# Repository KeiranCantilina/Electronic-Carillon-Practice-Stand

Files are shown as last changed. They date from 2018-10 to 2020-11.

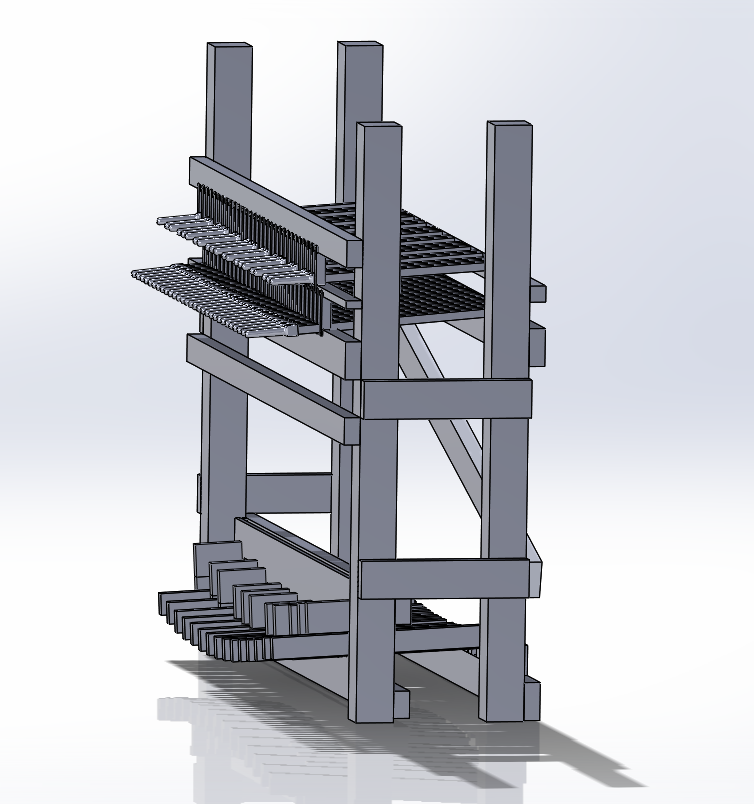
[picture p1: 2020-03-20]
mockup 2.PNG

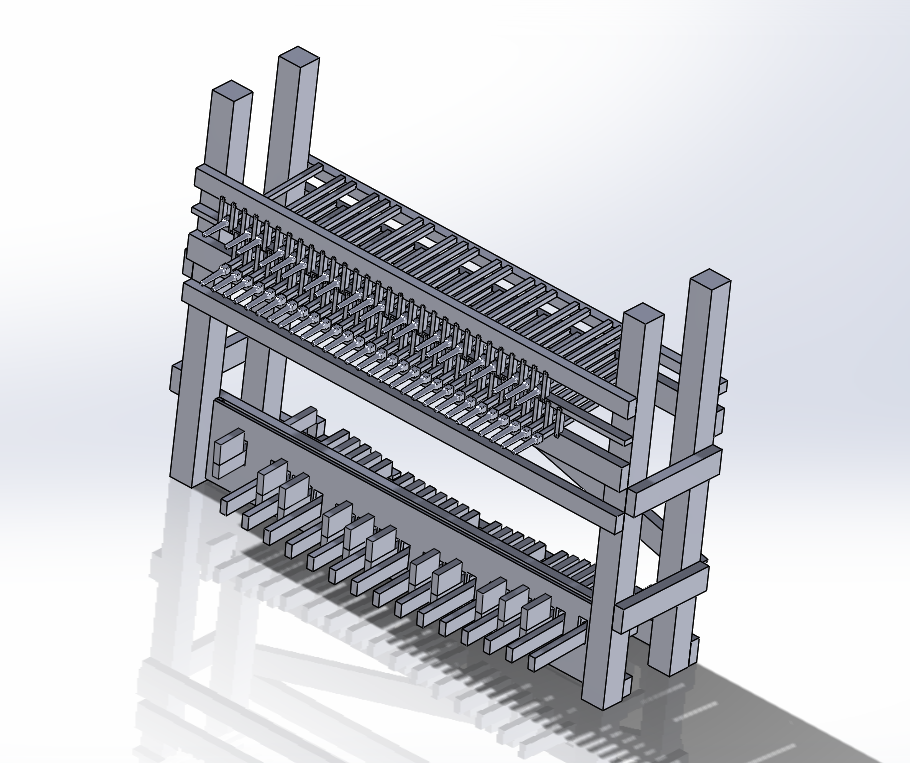
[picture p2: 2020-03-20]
mockup 1.PNG

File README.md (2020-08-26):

# Electronic Carillon Practice Stand
Development of an electronic carillon practice stand with improved dynamic sensitivity and low construction cost.

The performance goals of this project will be considered achieved if a 4-octave digital instrument is built with superior and adjustable dynamic sensitivity compared to existing commercial solutions. Good control of tremelando must be possible. 
The cost optimization goals of this project will be considered complete if the construction is finished at a total cost under $1000 USD (including the cost of purchasing the tools).

The design uses dimensional lumber for the frame and #4 steel rebar for keyweights to reduce costs. 
Given my lack of woodworking or machining skills (and lack of space/money for tools to develop such skills), custom parts are designed to be 3D printable using any low-cost hobbyist 3D printer. All other parts are sourced either online (Ebay, Amazon, Aliexpress, etc.) or at Home Depot.

For the frame, no tools are strictly required other than a handsaw, hacksaw, screwdriver, and measuring tape (unless you count the 3D printer). However, an impact driver saves a lot of time when putting screws in, and 42" Harbor Freight bolt cutters rigged with a double tackle make much quicker work of cutting rebar than a hacksaw. A cheap plastic miter box ($10 at the time of writing) is also helpful.

The current electronic design uses an Arduino Mega 2560 development board, ADS1118 analog-to-digital converters, and SS49E Hall Effect sensors paired with magnets to sense velocity (using magnetic field strength measurements as a proxy for position). A soldering iron is necessary to assemble the electronic components (for now, until I get PCB designs set up after which "toaster oven reflow" might be possible).

The microcontroller sends out MIDI messages over serial-USB to an ancient netbook running virtual midi port software and a sequencer (SyFonOne loaded with a custom soundfont made with recorded samples).

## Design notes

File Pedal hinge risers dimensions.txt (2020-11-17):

pedal riser dimensions (mm)

Total number of pedals: 27; need 27*24 inches of 1x2 (648", 54 feet)
For: Pedal width: 19 (needs to expand to 30mm with pads)
	Pedal Height (diatonic): 50.8 (actually 38)
	Pedal Height (accidental): 76+38 (3in + 1.5 in)
	Pedal Length (diatonic): 568 (nearly 24 inches)
	Pedal Length (accidental): 454
	Pedal Left Margin (to center of G): 85.45
	Pedal Linear Spacing: 45.23
	C to C: 1266.55
	Slot Size: 85.68 (unpadded)
	Keyfall at spreader: 85.68-38 = 47.68 (will need padding to match manuals)
	Foot contact part length: 110

Radius: 18mm (dia. 36)
CHANGE TO: width 19, length 36, holes for hinge screws and mounting screw
G: 59
Bb: 53
C : 35
C#: 29
D: 24
Eb: 19
E: 14
F: 6
F#: 3
G: 1.5
Ab: 0
A: 0
Bb: 0
B: 0
C: 1.5
C#: 3
D: 6
Eb: 9
E: 14
F: 24
F#: 29
G: 35
Ab: 41
A: 47
Bb: 53
B: 59
C: 71

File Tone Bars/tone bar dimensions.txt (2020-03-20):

Aluminum 6061
3/4in width, 1/8in thickness
(19.05mm, 3.175mm)

12 in 		177.52Hz TEST

Bb2	116.5409Hz	14.8074 inches		8.14407 inches between holes
C3	130.8128Hz	13.9764 inches		7.68702 inches between holes
C4	261.6256Hz	9.8827 inches		5.435485 inches between holes
C5	523.2511Hz	6.9864 inches		3.84252 inches between holes
C6	1046.502Hz	4.9389 inches		2.716395 inches between holes
C7	2093.005Hz	3.4898 inches		1.91939 inches between holes

Centers of keys are 23mm apart
Resonators: 3/4in. CPVC Charlotte Water Pipe (0.715" ID, 0.875" OD)(18.161, 22.225)
Test length: 652.8569 mm (25.70303")[130.8Hz] (adjustable to 662.0045 mm (26.06")[129Hz])
Test key length 2: 178.17592mm [523.25Hz] Pipe: 161.15544mm (cut short)
Use with 3/4 in. CPVC CTS Slip Cap Fitting

VERSION 2 ------------------------------

Bb2 to B4 uses 1/16" thick 3/4" wide aluminum bar.

Bb2	116.5409Hz	265.9888 mm		59.5814912 mm from ends
C3	130.8128Hz	250.952 mm		56.213248 mm from ends
B3	246.9417Hz	182.753 mm		40.936672 mm from ends

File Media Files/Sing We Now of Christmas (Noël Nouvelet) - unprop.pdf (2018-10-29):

2 & 4
b
b ∑ | ∑ | ∑ | ∑ | n | n

SingWe Now of Christmas (Noël Nouvelet)

15th Century French
Arr. KKC '15
œ œ | œ œ | œ œ | œ œ | œ

œ
œ

œ œ œ
œ

œ œ

œ™ œ
œ œ | œ œ
Œ | œ

œ
œ

œ œ œ œ
œ

œnœ
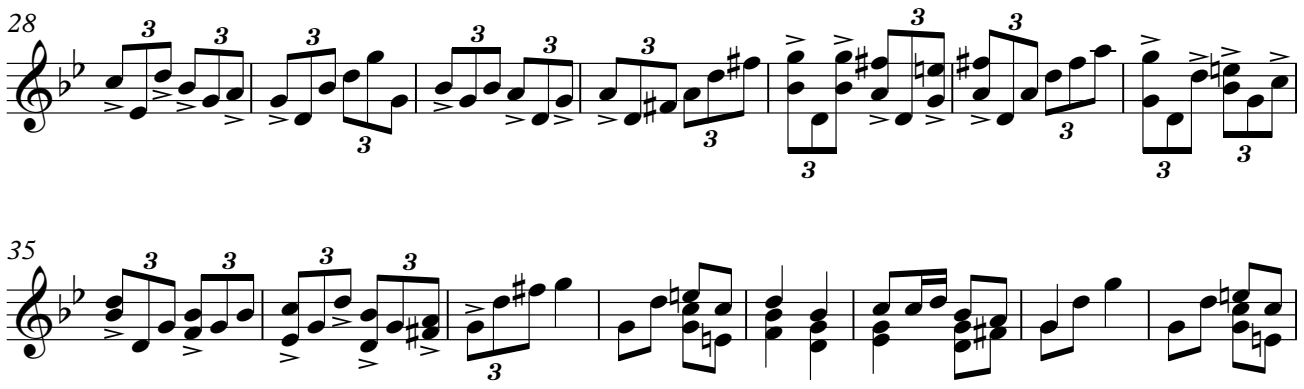
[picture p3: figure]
œœœœ œ; œ œœœ œ

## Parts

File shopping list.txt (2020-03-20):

Shopping List

4* 2x4x10 (cut in half) for posts
4* 2x4x8 for front and side struts (each cut at 70.386 inches, both pieces kept)
1* 2x4x8 for crossbar in back (cut to 6 ft-ish)
3* 2x3x8 for pedalboard, side, and back struts (cut 70.386 inches, as usual)
3* 1x2x8 for key separator, tone bar support, and hammer fulcrum bar (two cut 15.75 in[rest kept], 1 cut 70.386 inches))
1* 2x2x8 for accidental keys hinge base bar (normal 70.386 in cut)

Optional:
1* 4x8 sheet of 1/4" plywood for tone bars (cut down to two 2 x 5.25 foot pieces)
(really what is needed is 7.37" by 5'-3.4" sheet and a 3.87" by 5'-3.4" sheet)
1* 2x4 sheet of 1/2" sanded plywood for pedal keyspreader (cut down to 1ft x 4ft)
(1x3 foot sheet is better for pedalboard)

Lumber Cost
4*4.18	16.72
5*3.02	15.10
3*2.08	06.24
3*2.19	06.57
1*1.98	01.98
--------------
TOTAL:	46.61

Plywood
1*15.22

70.3858268
15.748

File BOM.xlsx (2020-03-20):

Quantity | Item | Price per each | Total Price | Notes | Bought Yet?
1 | 1lb #9 2-1/2" T25 bit wood screws | $10.30 | $10.30 | General assembly screws | Yes
1 | 2-pack of Bosch T25 impact driver bits | $2.38 | $2.38 | I might not actually need these, whoops | Yes
1 | 3/4"x1/8"x3' Aluminum flat bar | $10.00 | $10.00 | Estimated. For tone bar test | Yes
1 | 3/4"x1/16" Aluminum flat bar | $4.58 | $4.58 | Estimated. For tone bar test | Yes
1 | 3/4"x10' CPVC tube | $5.12 | $5.12 | Resonator tube test | Yes
2 | 3/4" CPVC cap | $0.34 | $0.68 | Cap of tubes for test | Yes
2 | Jorgenson 4-in bar clamp | $4.98 | $9.96 |  | Yes
1 | Miter box and saw set | $10 | $10.00 |  | Yes
4
TOTAL | $53.02
YTD | 53.02
Left2Buy | 0

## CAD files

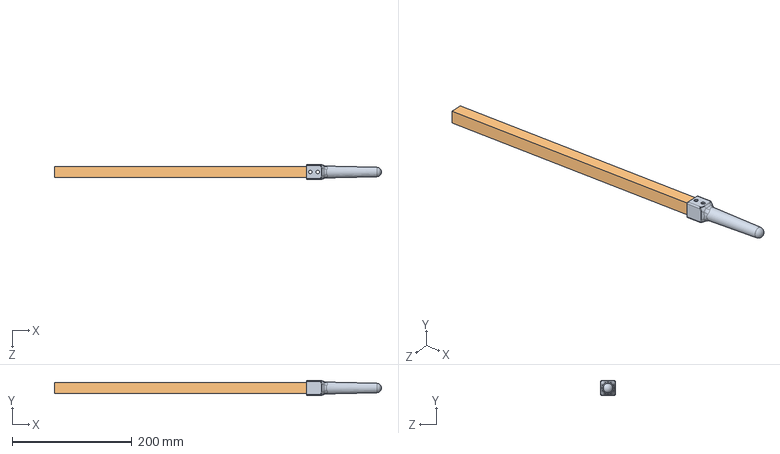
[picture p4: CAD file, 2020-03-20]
Frame/Baton test assembly.SLDASM
546.0 x 25.0 x 25.0 mm
baton
short key stick

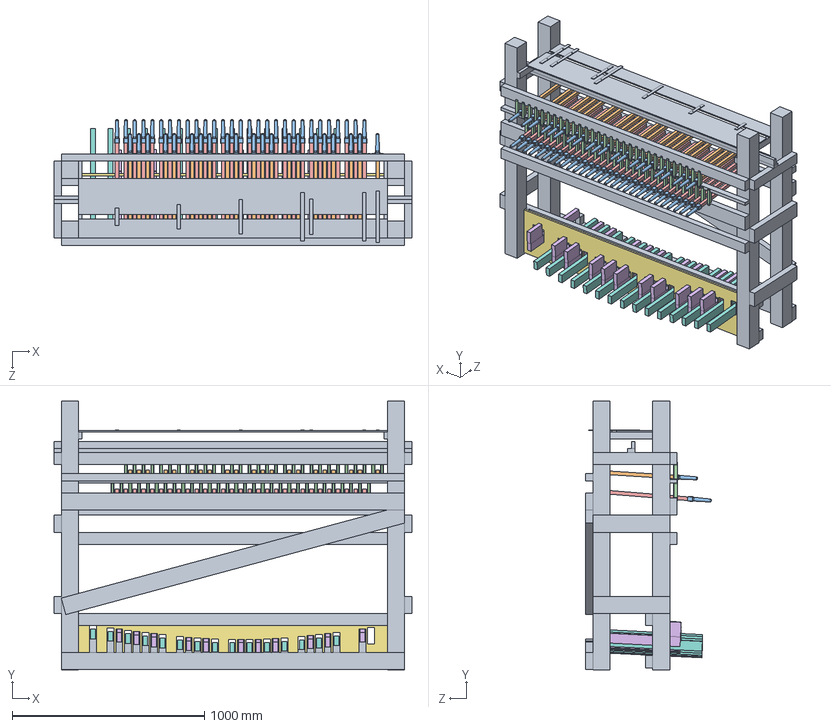
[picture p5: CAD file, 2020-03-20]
Frame/Preliminary test assembly.SLDASM
1863.8 x 1400.0 x 654.5 mm
diatonic keybase
short key stick x 21
baton_alternate x 50
baton spacer x 60
long key stick x 29
short pedal x 11
pedal keybase
long pedal x 15
tone bar mockup_version 3

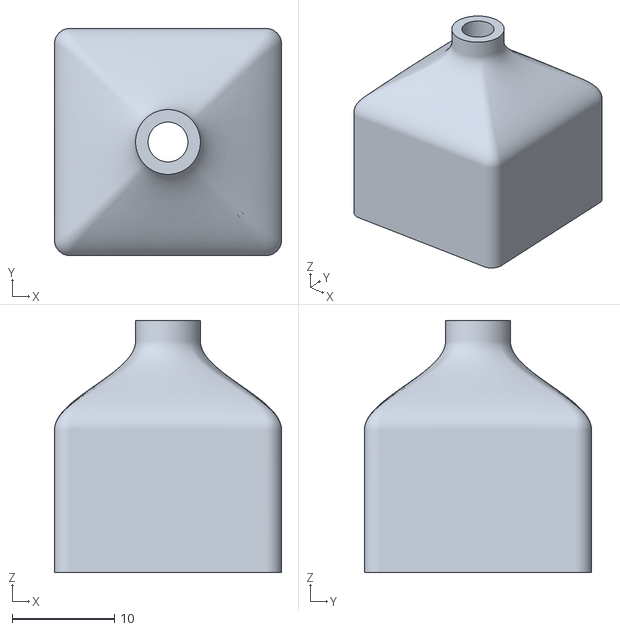
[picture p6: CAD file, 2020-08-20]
3D Printed Components/Hollow Baton Drilling Guide.stl
22.2 x 22.2 x 24.7

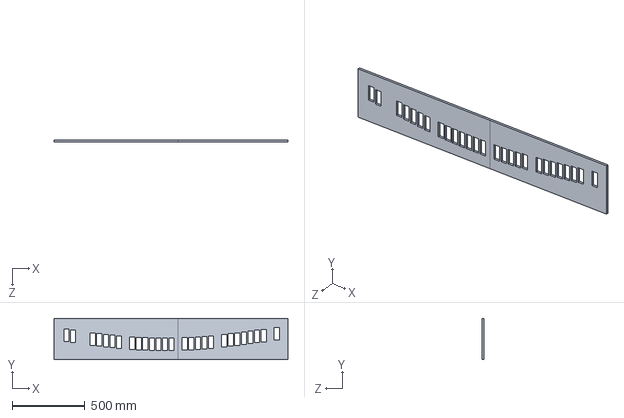
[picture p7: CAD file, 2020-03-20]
Frame/pedal keybase_split1.SLDPRT
1609.8 x 284.7 x 12.7 mm

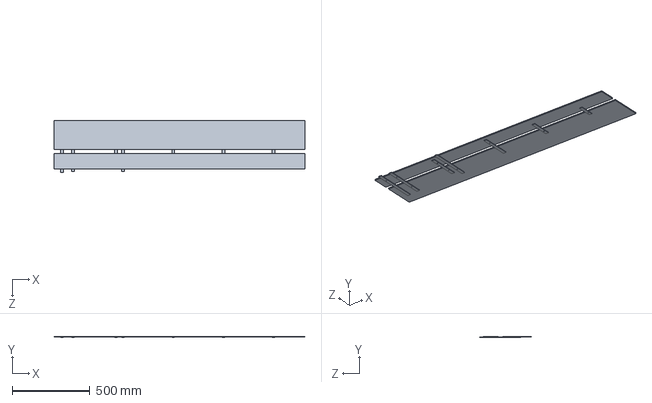
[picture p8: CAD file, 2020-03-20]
Tone Bars/tone bar mockup_version 3.SLDPRT
1610.2 x 9.53 x 333.0 mm

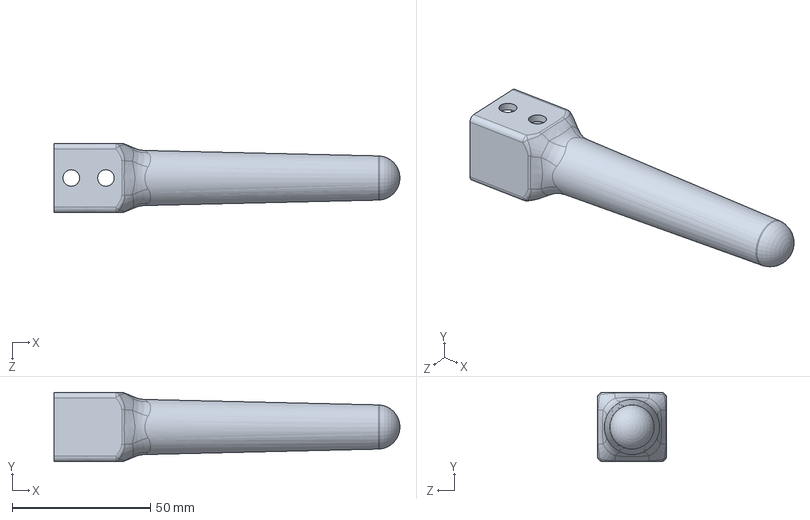
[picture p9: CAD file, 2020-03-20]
Frame/baton.SLDPRT
125.0 x 25.0 x 25.0 mm

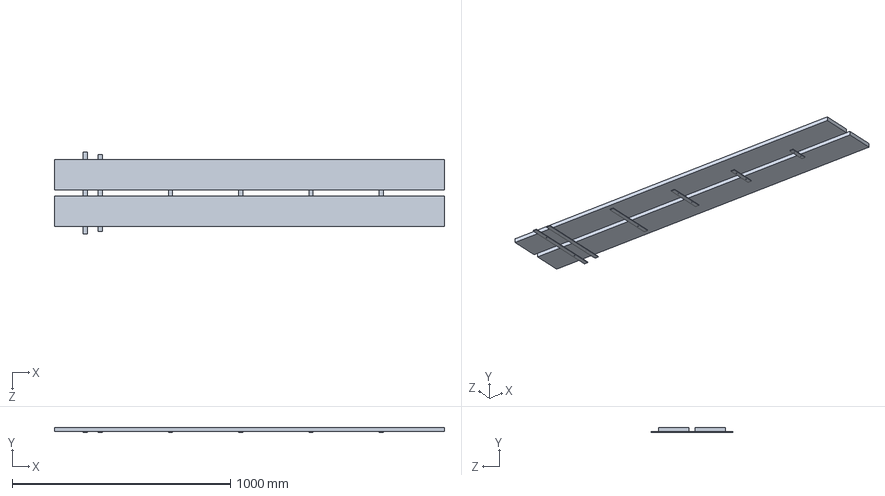
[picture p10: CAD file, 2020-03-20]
Tone Bars/tone bar mockup.SLDPRT
1788.2 x 22.2 x 376.1 mm

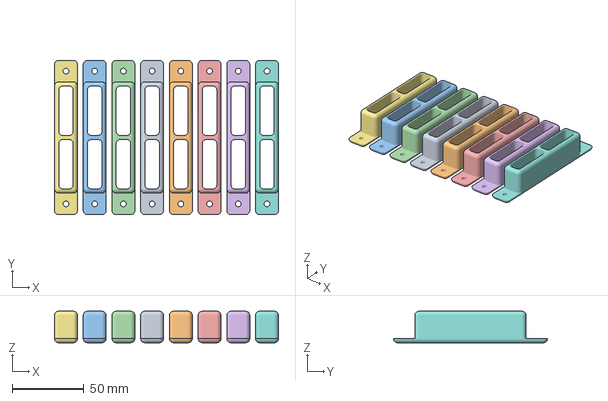
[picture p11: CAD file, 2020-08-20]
3D Printed Components/8X Accidentals Baton Spacer V1.3mf
156.0 x 107.5 x 22.0 mm
Accidentals Baton Spacer V1.stl x 8

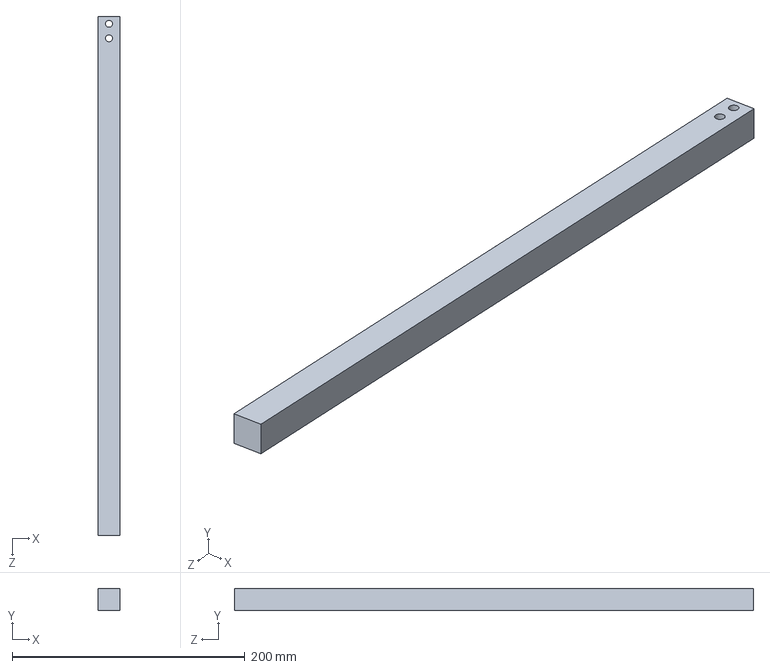
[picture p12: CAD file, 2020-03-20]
Frame/short key stick.SLDPRT
19.0 x 19.0 x 446.0 mm

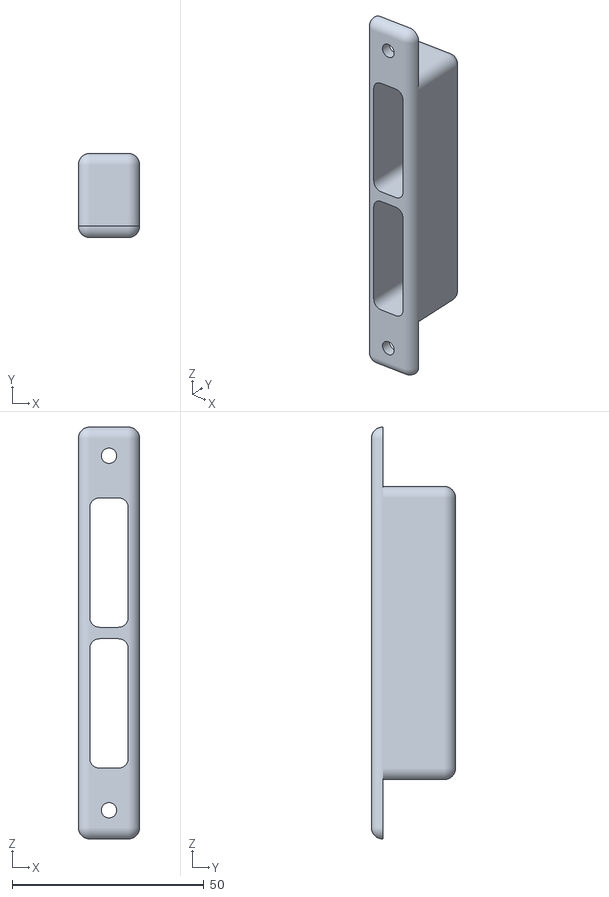
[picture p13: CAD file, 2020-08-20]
3D Printed Components/Accidental Baton Spacer V2 (short).stl
16.0 x 22.0 x 107.5

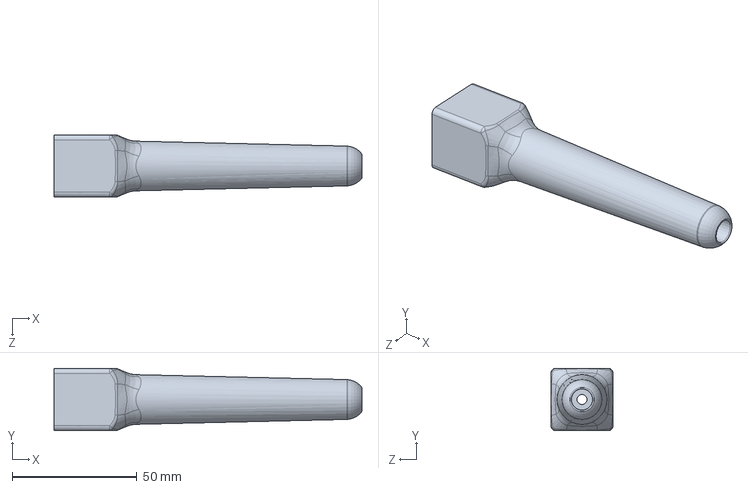
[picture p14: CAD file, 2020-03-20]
Frame/baton_alternate.SLDPRT
123.4 x 25.0 x 25.0 mm

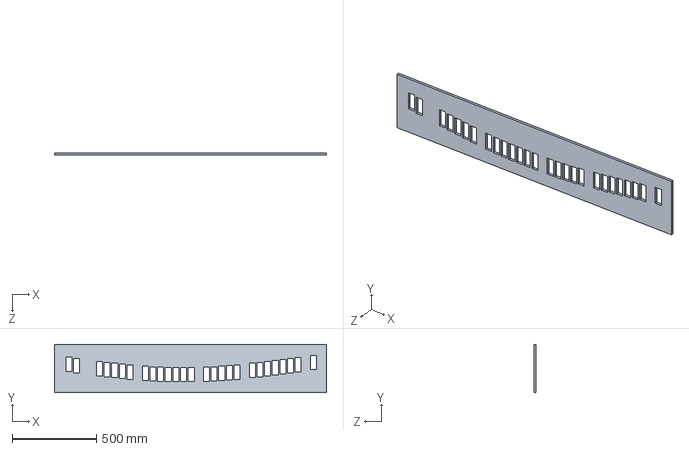
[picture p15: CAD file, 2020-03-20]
Frame/pedal keybase.SLDPRT
1609.8 x 284.7 x 12.7 mm

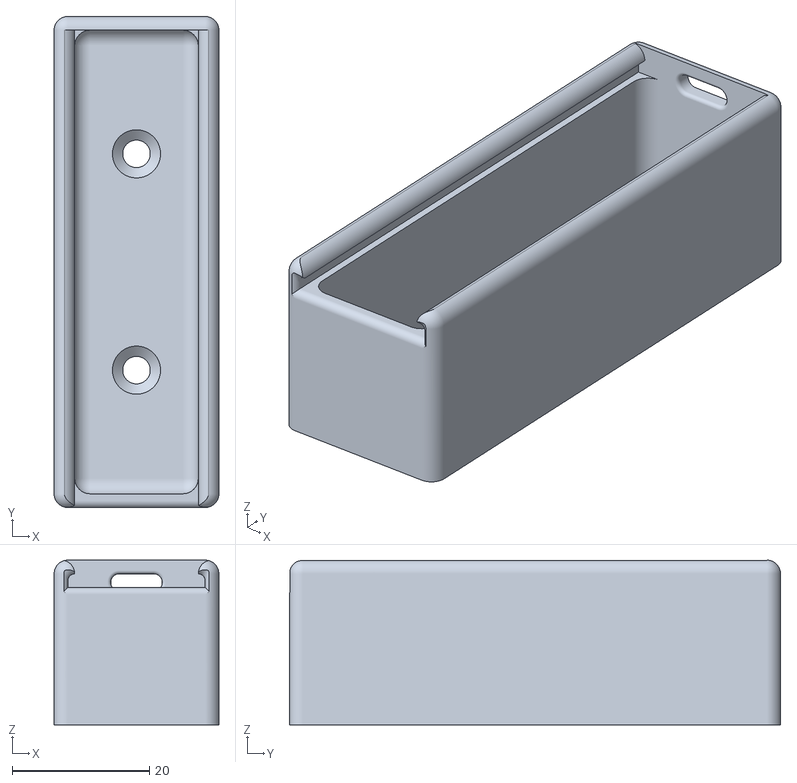
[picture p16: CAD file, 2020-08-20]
3D Printed Components/Weight Container V4.stl
24.0 x 71.5 x 24.0

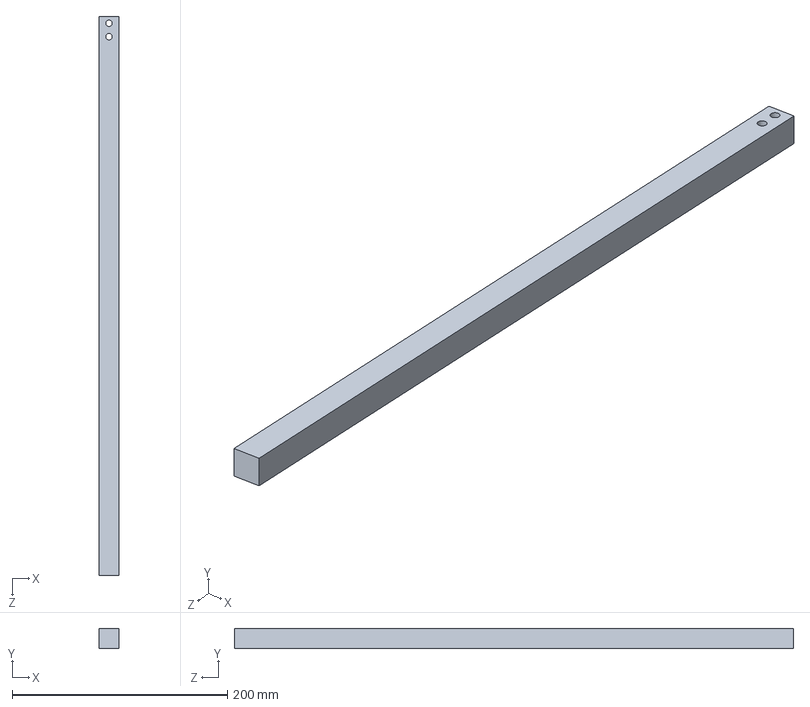
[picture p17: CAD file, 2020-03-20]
Frame/long key stick.SLDPRT
19.0 x 19.0 x 519.0 mm

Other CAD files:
Construction files and doc/batons.dwg
Frame/pedal layout ref.dwg
Frame/keyboard facade_openable.dwg
3D Printed Components/Sensor Holder Test.stl
3D Printed Components/Accidentals Baton Spacer V1.stl
3D Printed Components/Baton Fit Test.stl
3D Printed Components/Baton Hinge Mount V1.stl
3D Printed Components/Baton Hinge Mount V2.stl
3D Printed Components/Baton Spacer Drilling Guide.stl
3D Printed Components/Diatonic Baton Spacer V1.stl
3D Printed Components/Lid Weight Container V1.stl
3D Printed Components/Lid Weight Container V2.stl
3D Printed Components/Lid Weight Container V3.stl
3D Printed Components/Lid Weight Container V4.stl
3D Printed Components/Sensor Holder Test V3.stl
3D Printed Components/Sensor Holder V4.stl
3D Printed Components/Sensor Holder V5.stl
3D Printed Components/Sensor Holder V6.stl
3D Printed Components/Solid Baton V1.stl
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

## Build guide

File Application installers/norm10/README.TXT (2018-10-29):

Readme.txt

(****************************************)
(*                                      *)
(*        SHORT NOTICE                  *)
(*                                      *)
(* Developement of this program is up   *)
(* you! (users) If you want something   *)
(* new you have to send E-Mail. I have  *)
(* few cool ideas, but I don't code 'em *)
(* if there is no users. Let me know if *)
(* you exist :=)                        *)
(*                                      *)
(* -Tommi- The Grape -                  *)
(****************************************)

The WavNormalizer 1.0.4 , build 205 (18. July 2000)
	
	- Now you really can minimize program while process.

The WavNormalizer 1.0.4 , build 204 (17. May 2000)

	- Support for Lame encoder now build in feature.

The WavNormalizer 1.0.4 , build 201

	- "Nag" screen now really is destroyed after "OK"

The WavNormalizer 1.0.4 , build 200
	
	- Corrected many GUI-based bugs
	- Added some GUI features
	- Simplifyed external encoder support
	- Added BladeEnc encoder profile
	- Lots of cleanups to code
	- Correct LinearTeam homepage link

The WavNormalizer 1.0.3 , build 172

	- Corrected startup bug on WinNT with
	  user right.

The WavNormalizer 1.0.2 , build 168

	- Added external command line encoder support
	- Fixed some minor bugs
	- Some minor changes

The WavNormalizer 1.0.0 , build 147
	
	- Optimized normalizatiom engine
	- Rewritten user interface
	- Added 'Normalize' command registration
	  for .Wav files

The WavNormalizer 0.7 PreRelease 3, build 217

	-Huge "What the hell I was thinking about" bug corrected.
	 There was about a 50% chance that a Normalized file was 
	 visited by the "Kellog's Snap, Crackle & Pop" team.
	-My apologies.

The WavNormalizer 0.7 PreRelease 2, build 210
	
	-Wave format bug corrected.

The WavNormalizer 0.7 PreRelease 2, build 208

Content of this file:
	
		Description of program
		System requirements
		Using the program
		License
		Contacting me
		Thanks to
		DISCLAIMER

PROGRAM DESCRIPTION:

	WavNormalizer is a program which will maximize the
	volume of (normalize) Microsoft wave (.wav) files,
	so that they all play at the same volume level. 

	The .wav file has to be 8bit or 16bit wave in PCM
	format in any sample rate, mono or stereo (which is
	actually a normal wave in normal format).

	WavNormalizer normalizes .wav files into themselves,
	therefore no extra hard disk space is needed. However,
	if your system crashes (or if you have a power outtage)
	during the normalization process, the wave file will
	most likely be corrupted. WavNormalizer is quite fast
	(milliseconds in most cases... but minutes could be
	required for files 800Mb or so in length), so the
	risk is really quite small when compared to the
	benefits that you achieve. To be safe, though, you
	might want to copy cherished/irreplaceable .wav files
	to a "working" directory as you modify them, just
	in case.  This action, of course, falls under the
	"common sense" directive as mandated by the ABC
	(Active Brain Cell) branch of life itself. 

System requirements:

        WavNormalizer requires Windows9x, WinNT 4.0 or Win2K.

Using the program:

	In my opinion, this program is so easy to use that
	it doesn´t need any specific help files. Just click
	on "Add files to list" and select the path/file(s)
	that you want to normalize or drag and drop files on
	window.  Then, simply click on the "Go" button.

	Under the Preferences tab, you can select the
	percentage of Normalization by changing the default
	value of 100.0% (either manually by double
	clicking/changing the value, or by using the
	up/down arrows).

	If "Quick Norm" is selected, then WavNormalizer
	will automatically Normalize any .wav file that
	you Drag and Drop onto the program icon.

	If "Hide main window" is selected, then WavNormalizer
	will not show main window during normalization
	(this option requires "Quick norm" option to work).

	Under Enc tab, you can define command line for
	external program. Normalizer will send file to
	program just after normalization. There is few
	details you need to know about how this encoder
	options will effect to commandline.

	Encoder path: 
	
		Path and file name that points your
		encoder executable (.exe) file.

	Encoder command line options:

		This is the "prototype" for your
		commandline that will be formatted
		by normalizer. There is couple things
		you need to put there.

		%inf variable: This variable is
		replaced with normalized file's
		path and name
		
		%outf variable: If you need to
		declare output file name for encoder

	(Like -i:%inf -o:%outf -a - c -SomeOptions ...)
	%inf and %outf variables must be written exactly
	like that (Small letters). You have to declare
	%inf variable!	

	Filename options:

	Extension: If you need to change outfile extension
	it will be replased with extension declared in here

	You can save this settings and and it to ready to
	roll profiles. It is handy if you use more that one
	encoders. (Please send me working profiles via E-mail.
	just send copy of ltn1.ini to me please.)

Licence:

	This program is free for use of any kind. If you
	like and/or use this program, please send me a
	postcard or contact me via Email at the address
	below (or you can contribute actual currency if
	you'd like!? :)

	You may distribute this program freely, as long
	as it is unchanged and includes all of the files
	listed below.

	Norm10.exe	Program
	Readme.txt	This file

Contacting me:

	If you have any suggestions, bugs, or comments
	pertaining to this program, I would be happy to
	hear from you. Here's how you can contact me:

	SnailMail:

		Send Email to find out.

	EMail:
	
		tommi.prami@kno.fi

Thanks to:

	Juha Hartikainen
		-Many programming hints.

	Edmond "Ed" L Lacoste III
		-Graphics design for program	

	JJ Richard
		-Major beta testing and his American
		 English language grammar corrections.
	
	Reijo "Reke" Tuononen
		-For cool (Programming) ideas and he's
		 professional touch :=)
	
	Marko Raninen
		-Many ideas pertaining to user interface.

	Sanna Antikainen
		-For lending me her copy of the Titanic Soundtrack
		(which helped me find that huge bug in build 210).

	all co-workers at KNO Oy...

DISCLAIMER OF WARRANTY: 
(I wish I didn't have to do this, but I must);

	THIS PROGRAM IS DISTRIBUTED AS FREEWARE, SO DON'T
ASSUME A WARRANTY OF ANY KIND. YOU USE THIS PROGRAM COMPLETELY
AT YOUR OWN RISK. DON'T ASSUME CORRECTNESS, ACCURACY OR RELIABILITY
OF ANY KIND WHEN USING THIS DISTRIBUTED SOFTWARE. ANY DAMAGE CAUSED 
BY THIS PROGRAM, WHETHER BEING FROM A DIRECT OR INDIRECT USE OF THIS 
PROGRAM, AS WELL AS TO ANY EQUIPMENT USED, AND/OR ANY MATERIAL IN IT,
IS SOLEY YOUR RESOPONSIBILITY.  THE RISK IS YOURS AND YOURS ONLY.
YOU AGREE TO ALL OF THESE TERMS BY STARTING THIS PROGRAM.  IF YOU 
DON'T AGREE WITH THESE TERMS, THEN DON'T USE THIS PROGRAM.

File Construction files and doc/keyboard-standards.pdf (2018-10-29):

## Appendix D GCNA Keyboard Standards

The following text is reproduced in its entirety from the GCNA Bulletin, November 1970, incorporating several corrections of errata. The standards described herein were adopted at the 1970 Congress and remain the recognized North American carillon clavier standard, except for modifications to the pedals which were approved in 1981. The text in italics has been superceded by revised standards adopted in 1981. The 1981 revisions were never published per se, but exist in the form of drawings prepared by Richard Strauss and dated 1981. Only those dimensions pertaining to pedal geometry were adopted. Copies of these drawings are on file at the Brees Library in Lake Wales, Florida. The drawings following these written standards attempt to graphically illustrate the standards adopted in 1970 and 1981.

Over the years since the adoption of these standards, some carillon designers and builders have introduced refinements and improvements in their claviers, in some cases deviating from the standards. The clavier design by Richard Strauss know as K2000, which incorporates European key spacing, has been used as the basis for several new claviers in the U.S. as well as Europe. These trends indicate that clavier design continues to evolve

## Carillon Console Standards of the Guild of Carillonneurs in North America July 1970

Text in italics superceded by revised standards adopted in 1981

Purpose: | The purpose of this standard is to specify dimensions and construction details for manual consoles of carillons installed in the United States of America and in Canada.
Scope: | This standard shall apply in detail to consoles of carillons of four-octave range. For carillons of more or less than four octaves, this standard shall apply as far as practical, consistent with the different range of the instrument.
1 | Range of Manual: The basic compass of the manual clavier shall be four octaves, c3 to c7. A key shall be provided for each bell in the carillon; all semi-tone keys should be provided within the compass of the instrument.1
2 | Range of Pedals: The basic compass of the pedal clavier shall be two octaves, C3 to C5 including a pedal corresponding to each manual key present within this compass; where bells lower than the basis keynote (the bell attached to c3 key and pedal) are present, extra pedals to control these bells shall be provided below the basic pedal compass.
3 | Lateral relationship of manual to pedal: A “playing axis” has been established in designing the standard keyboard: this axis shall be a vertical line joining the centerlines of the d5 manual key and the B3 pedal; in other words, the B3 pedal is to be located directly beneath the d5 manual key.
4 | The vertical distance from the centerline of “white” keys to top of “white” pedal at axis shall be 30 11/16 in. (779 mm.).
5 | Horizontal distance from front end of pedal to front end of “white” keys at axis shall be 1 3/8 in. (35 mm.).

6 | The vertical distance between centerlines of rows of “white” and “black” keys shall be 3 13/16 in. (97 mm.).
7 | Horizontal distance from front end of “white” key to front of “black” key shall be 2 3/4 in. (70 mm.).
8 | Horizontal distance between key centers shall be 2 in. (51 mm.).
9 | It is recommended that the “white” keys be no shorter than 24 in. (610 mm.), measured from the playing end to the fulcrum.
10 | The keys, when at rest, should be inclined upward slightly toward the playing ends; the centerline of each key should form an angle of 2°to a horizontal line drawn through the center of the key at the fulcrum.
11 | The distance from the front end of the “white” keys to the front surface of the key “spreader” should be not less than 7 ¼ in. (184 mm.).
12 | That untapered portion of the key which lies on the player’s side of the “spreader” shall have a cross-section of 1 in. x 1 in. (25 mm. x 25 mm.).
13 | The tapered playing-end of the key shall have a length of 3 3/8” in. (86 mm.).
14 | Shape of key playing end: The playing end of the key shall be nearly cylindrical, (actually, a truncated cone), being tapered in such a way as to have a diameter of 5/8 in. (16 mm.) at a point 1 ½ in. (38 mm.) from the end; it is suggested that this be produced by giving this portion of the key a diameter of approximately ¾ in. (19 mm.) at the end toward the untapered (square cross-section) portion and 9/16 in. (14 mm.) at the end toward the player. (This requirement, together with the key spacing detailed above, insures that there will be a clear space of 3 3/8 in. (86 mm.) at the measuring point for the hand to descend between the keys on either side of the one being played)
15 | The transition from the square to circular cross-sectional portions of the key shall be smoothed, to present no sharp corners.
16 | The end of the key shall terminate in a portion of a sphere whose diameter is no less than the diameter of the key at that point and no more that 1 ½ times this diameter.
17 | The depth of stroke of the key, measured at the front edge of the key “spreader” shall be 2 in ± 1/8 in. (51 mm. ± 3 mm.)
18 | It is recommended that the length of the “white” pedal at axis be not less than 22 5/8 in. (575 mm.) measured from the front end to the fulcrum.
19 | The top surface of the pedal, when at rest, shall make an angle of 2°with a horizontal line drawn through the top center of the fulcrum.
20 | The vertical distance from the top of the “black” pedal to the top of the adjacent “white” pedal shall be 3 in. (76 mm.). But note, that in the case of the pedals in the range where concavity is used, this distance shall be measured from the top of the “black” pedal to a point half way between the top surfaces of the adjacent “white” pedals.
21 | The horizontal distance between centerlines of adjacent “white” pedals shall be 3 ½ in. (89 mm.), measured at the end of the pedals nearest player. The “black” pedals shall be centered between adjacent “white” pedals.
22 | The width of the pedals shall be 1 3/16 in. (30 mm.).

23 | The effective length of the playing surface of the “white” pedal shall be not less that 4 ¾ in. (121 mm.) nor more than 5 in. (127 mm.), the former being recommended.
24 | The effective length of the playing surface of the “black” pedal should be not less than 4 in. (102 mm.) nor more than 4 ¼ in. (108 mm.), the latter being recommended. N.B.: this dimension shall not overlap the preceding (no. 23) by more than ¼” (6 mm.).
25 | The depth of stroke of the pedal, measured at the pedal “spreader”, shall be 2 in. ± 1/8 in. (51 mm. ± 3 mm.).

26 The pedal clavier (having a compass as detailed in point no. 2 above) is to have a slight
| radiation at the top of the compass and a greater radiation at the bottom. In the case of a four-octave console with no additional pedals below the basic keynote, this radiation is to be as detailed in the accompanying prints; the angle and equivalent radii (approximate) from which these prints where drawn are listed in Table I below:

Table I
Pedal Radiation

Left Radiation
Note | Angle | Equivalent Radius
F#3 | 1 1/2° | 67 ½ in. (1,715 mm.)
F3 | 2° | 61 ½ in. (1,562 mm.)
E3 | 7° | 55 ½ in. (1,410 mm.)
D#3 | 10 1/2° | 49 ½ in. (1,257 mm.)
D3 | 14° | 43 ½ in. (1,105 mm.)
C#3 | 19° | 37 ½ in. (953 mm.)
C3 | 23° | 31 ½ in. (800 mm.)

Right Radiation
Note | Angle | Equivalent Radius
F4 | 2° | 61 ½ in. (1,562 mm.)
F#4 | 3° | 61 ½ in. (1,562 mm.)
G4 | 4° | 61 ½ in. (1,562 mm.)
G#4 | 5° | 61 ½ in. (1,562 mm.)
A4 | 6° | 61 ½ in. (1,562 mm.)
A#4 | 7° | 61 ½ in. (1,562 mm.)
B4 | 8° | 61 ½ in. (1,562 mm.)
C5 | 10° | 61 ½ in. (1,562 mm.)

N.B.: “Angle” is that made by one side of the pedal with a line normal to the pedal “spreader” which passes through the point on that side of the pedal opposite the fulcrum. “Equivalent radii” are measured along the extended centerline of the nearest unradiated pedal key and are measured from the front of the unradiated pedals.

27 The pedal clavier shall be concave, to a large radius at the top end of the compass, and a smaller radius at the bottom, and the concavity shall be similar and complementary to the radiation specified in item no. 26 above. For the four-octave console having no pedals below the basis keynote, the concavity shall be as shown in the accompanying prints, and given in Table II below:

Table II
Pedal Concavity
Left Concavity | | Right Concavity
Note | Elevation | Note | Elevation
F#3 | 1/8 in. (3 mm.) | F4 | 1/8 in. (3 mm.)
F3 | 3 1/6 in. (5 mm.) | F#4 | 1/4 in. (6 mm.)
E3 | ½ in. (13 mm.) | G4 | 3/8 in. (9 mm.)
D#3 | 7/8 in. (22 mm.) | G#4 | 9/16 in. (14 mm.)
D3 | 1 ½ in. (38 mm.) | A4 | 13/16 in. (21 mm.)
C#3 | 2 ¼ in. (57 mm.) | A#4 | 1 in. (25 mm.)
C3 | 3 1/16 in. (78 mm.) | B4 | 1 3/8 in. (35 mm.)
| | C5 | 2 1/8 in. (54 mm.)

N.B.: “Elevation” is the vertical distance of the top of the pedal, when at rest, above the tops of corresponding pedals (“black” or “white”) in the range to which no concavity is applied.
28 | The playing surface of the pedals should be made with a suitable material to minimize
pedal wear.
29 | For carillon consoles large than four octaves, the center axis shall remain the same as for
the four-octave carillon console.
30 | The wire adjusters used must reliably hold the adjustment selected by the carillonneur,
but must be readily capable of adjustment by the carillonneur using one hand while in front of the console.
31 | The wires connecting the “white” keys to the carillon should be attached to the key at a
point no less than 11 in. (279 mm.), or more than 12 in. (305 mm.), from the playing end of the key, and the wire connections to the “black” keys shall be attached at a point no less than 8 ¼ in. (210 mm.) and no more than 9 ¼ in. (235 mm.) from the playing end of the key.
32 | The music rack shall be at least as wide as the distance between the centers of the keys
at the extreme ends of the compass, shall tilt back as far as practical (without touching the wires), and shall not overhang the front edge of the key “spreader”. The height of the rack back shall be 14 in. (356 mm.). The angle between the back and the surface of the lip shall be 90°. The surface of the lip (or ledge) shall be at least 1 ¼ in. (32 mm.) wide, and no wider than 1 ¾ in. (44 mm.).
33 | The bench shall be adjustable for height, shall be provided with a footrest (located far
enough distant from the pedals to give good clearance when playing the pedals), and shall be at least as long as the distance between the last key “spreader” slot on the left and the last pedal “spreader” slot on the right.
34 | It is imperative that the console be constructed in a perfectly sturdy manner; of materials
of a high degree of durability and permanence; accurately to the dimensions given, and allowing an absolute minimum of “play” or waste motion; in such a manner and of such materials as to operate smoothly and reliably in all conditions, with a minimum of adjustment and upkeep; and at the same time, to be as noiseless as possible.

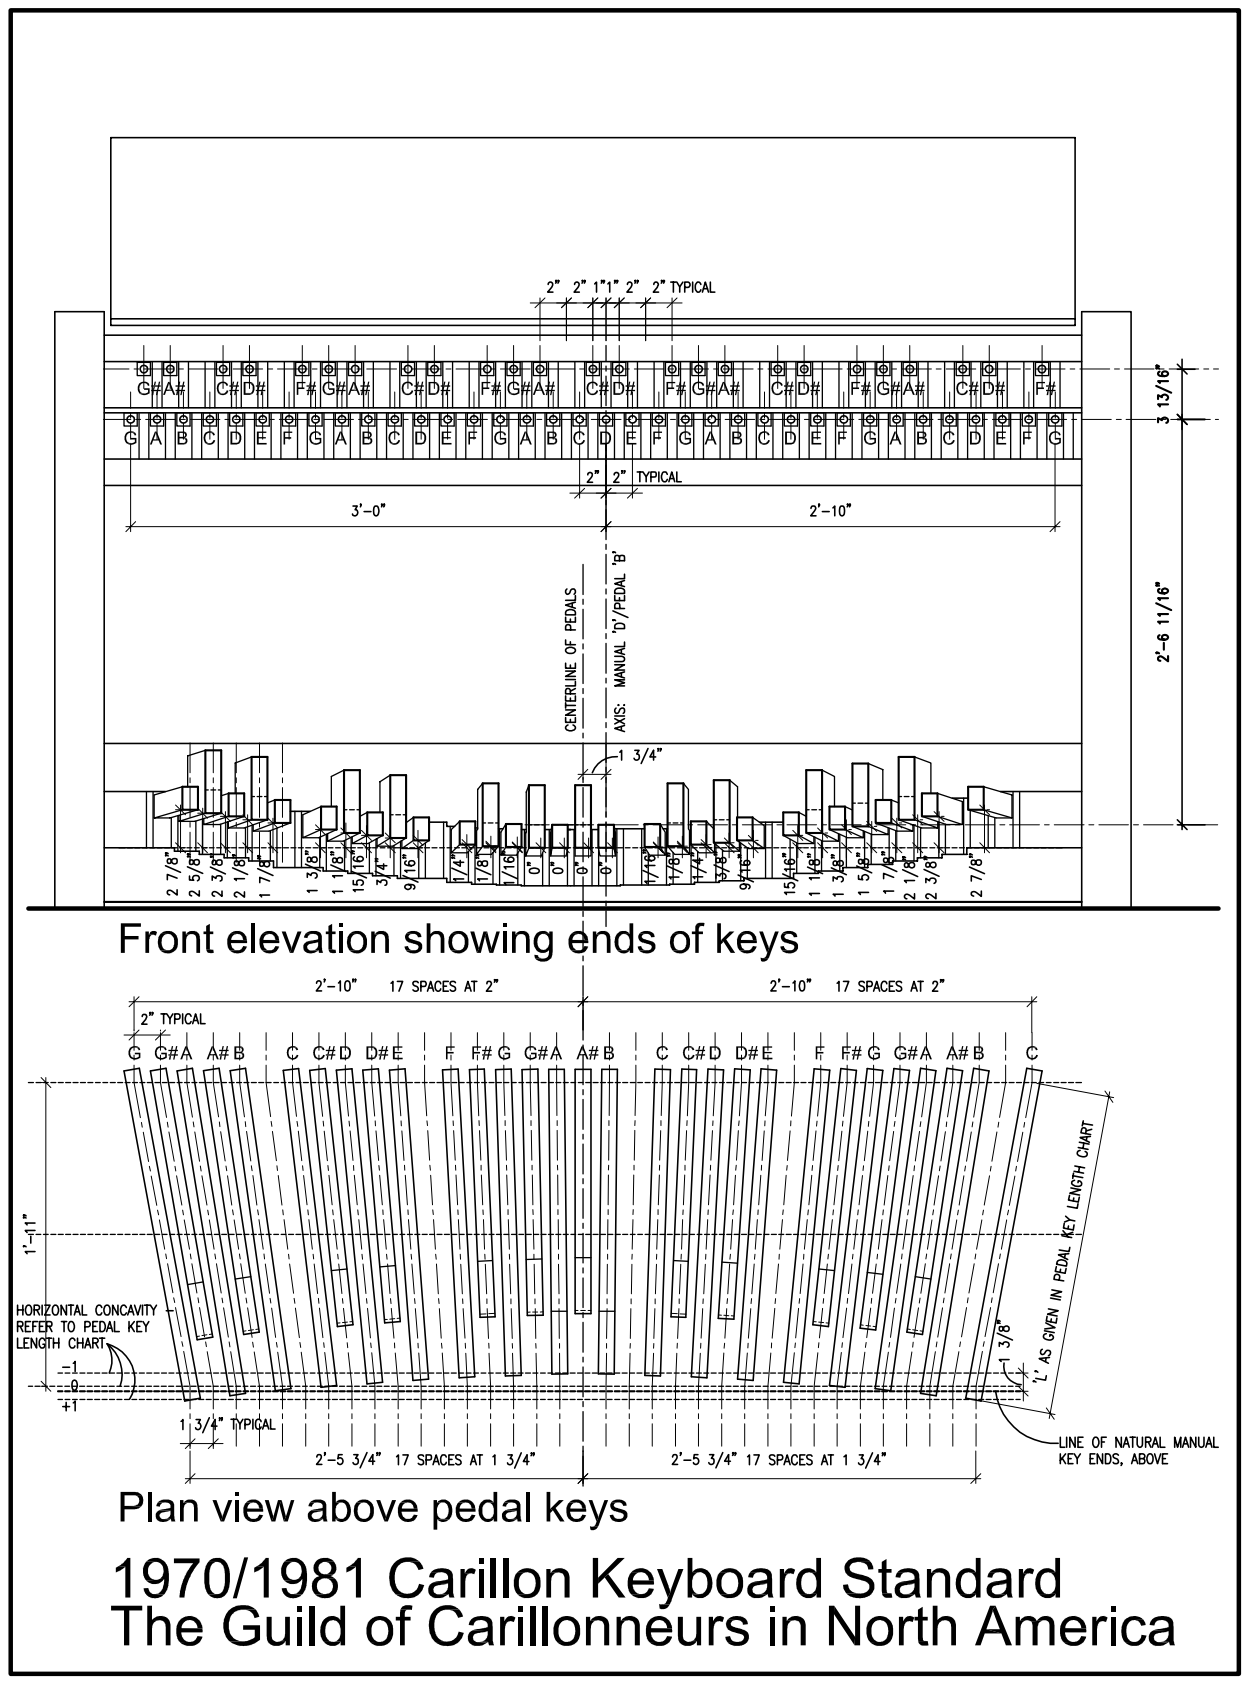
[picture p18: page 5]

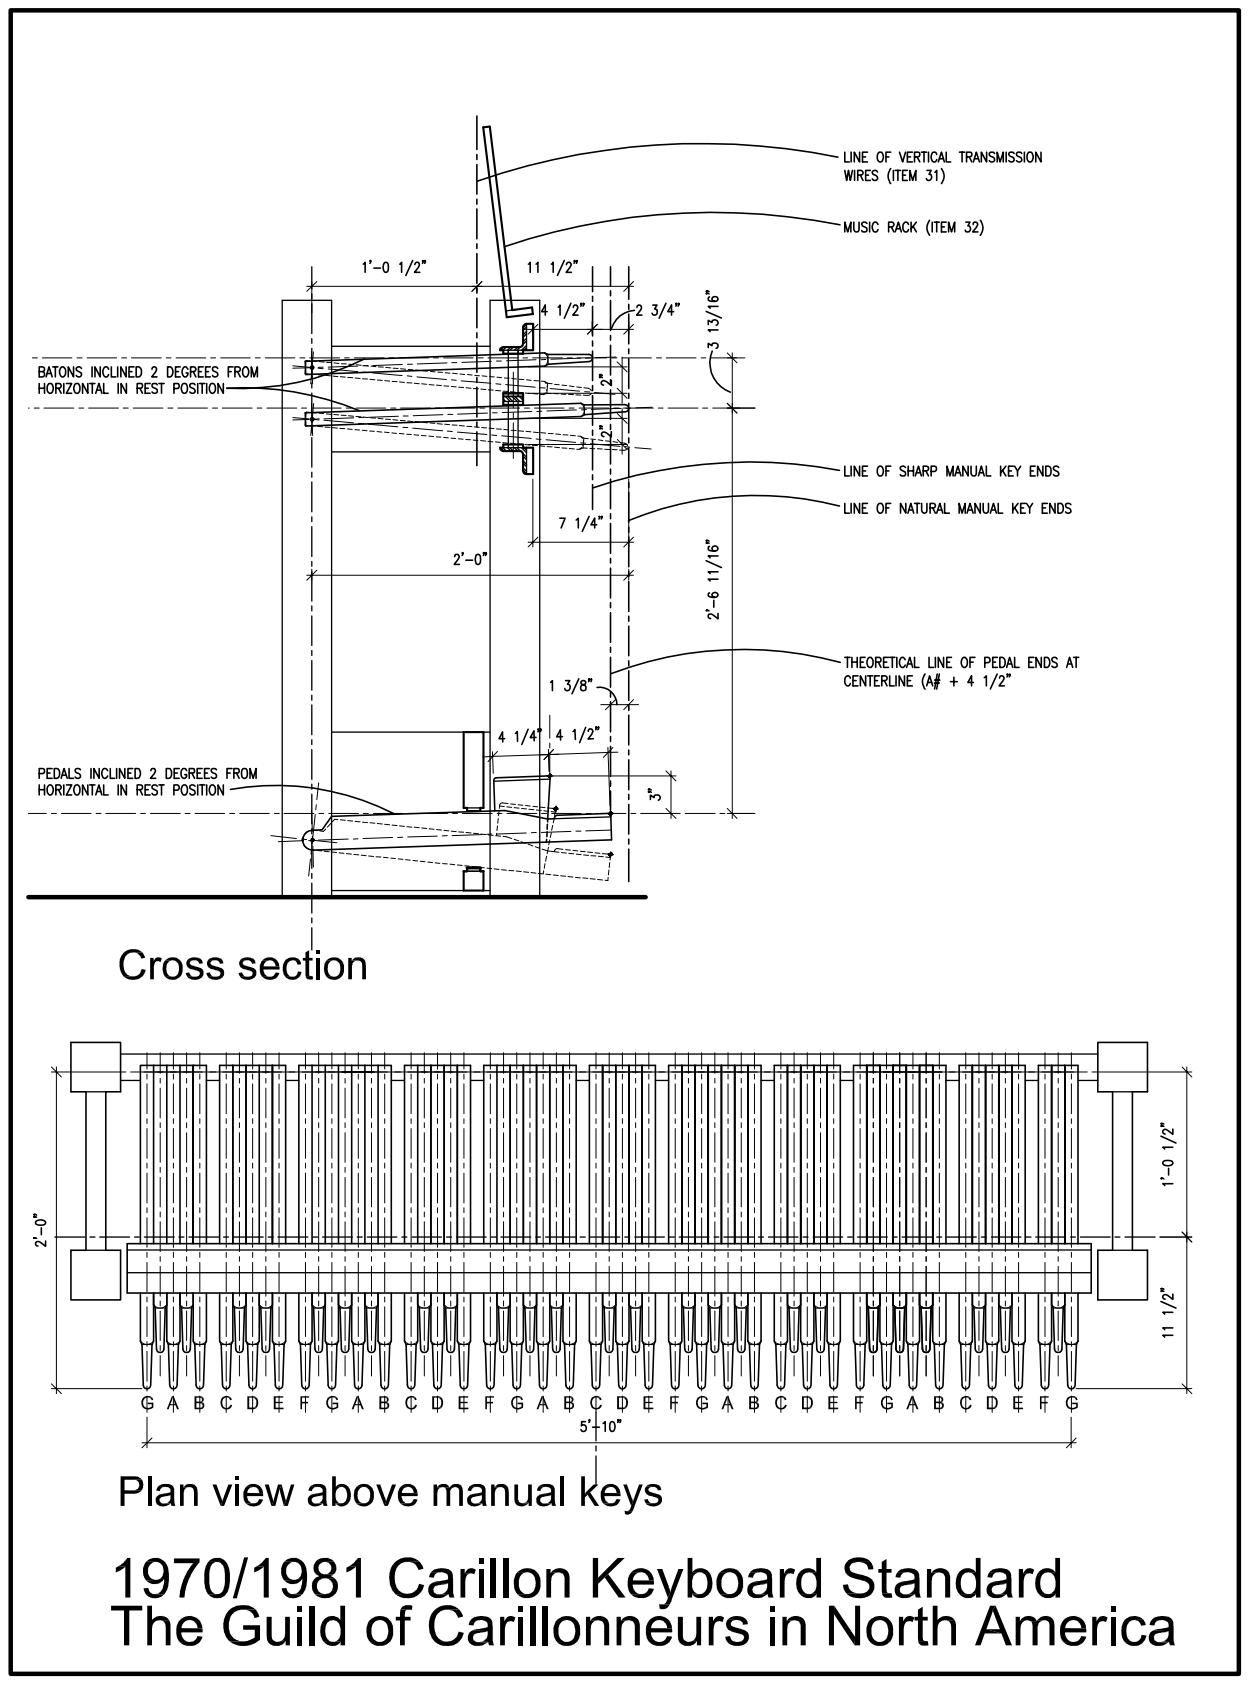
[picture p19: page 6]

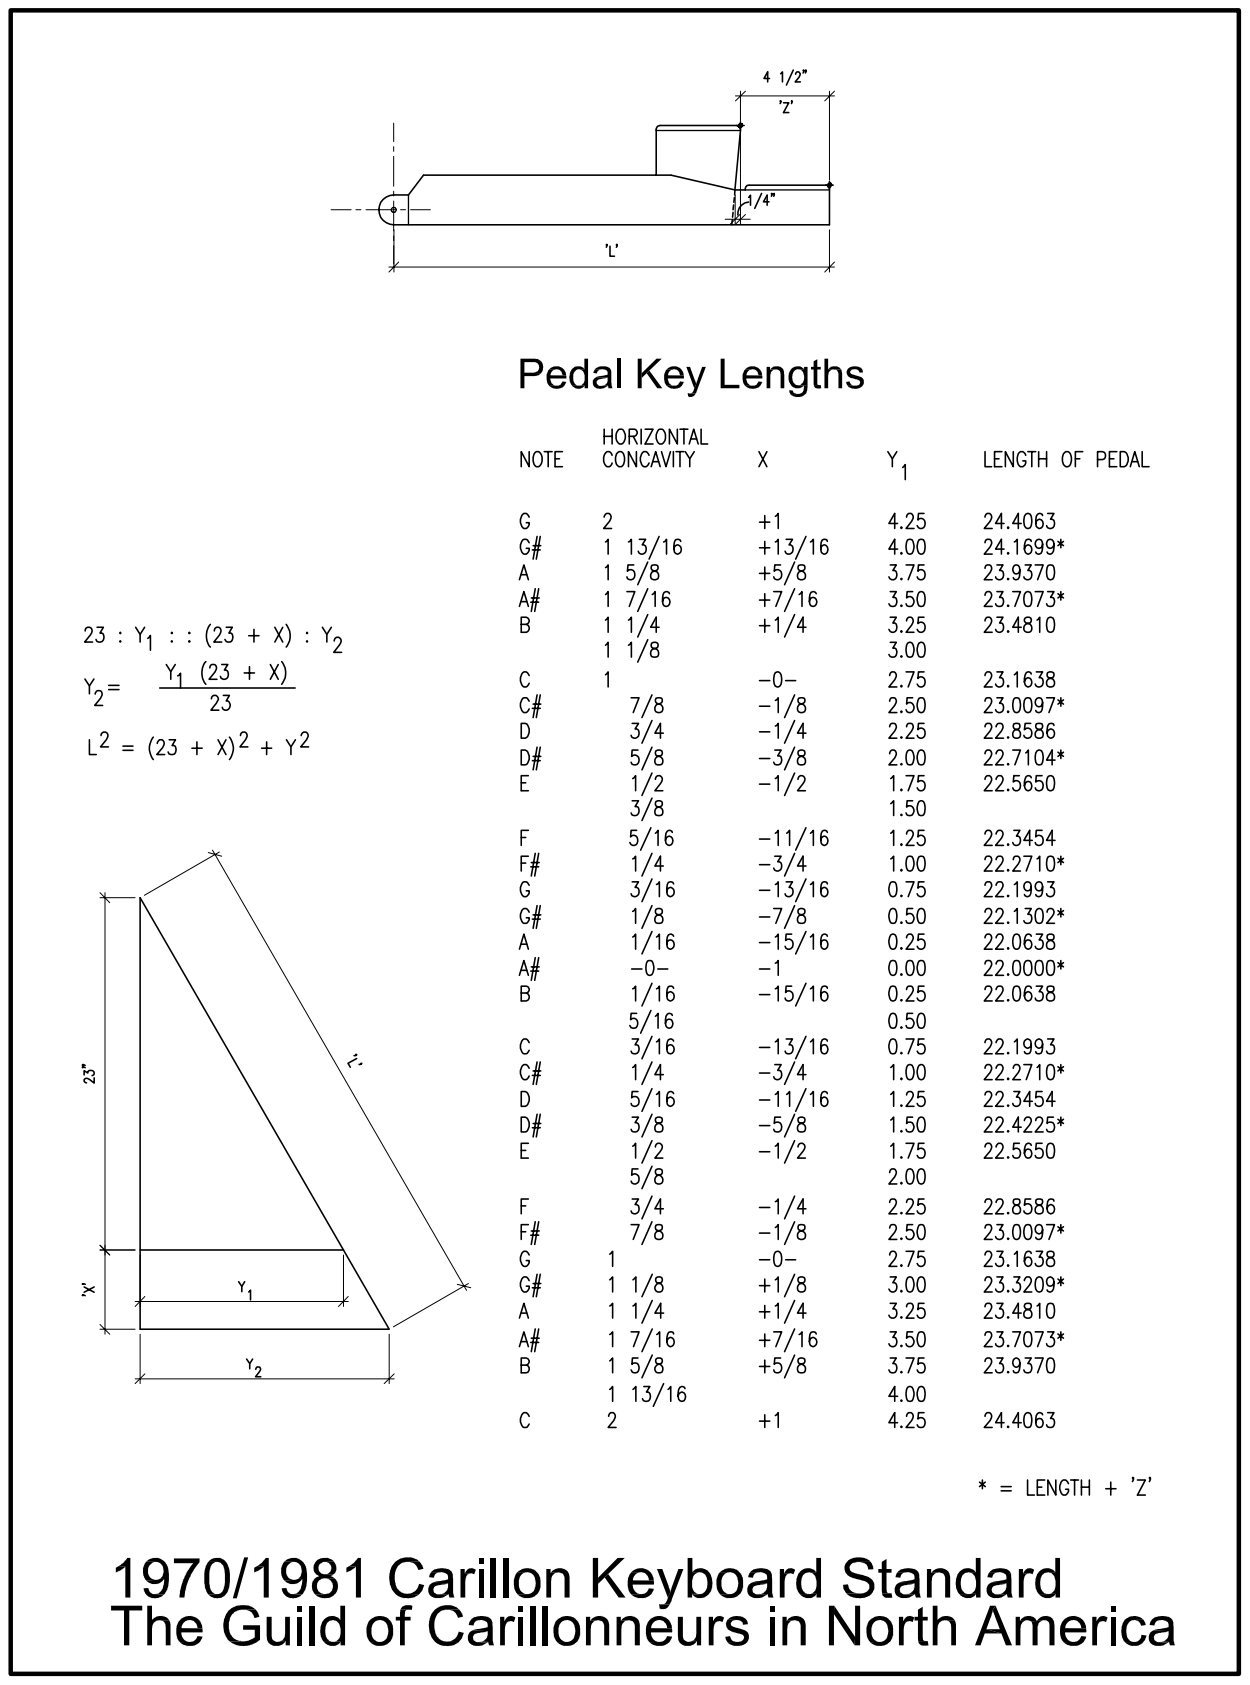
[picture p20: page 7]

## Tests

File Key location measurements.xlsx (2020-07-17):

Diatonic | Note | Accidental | Note | Spacing between keys
Left End |  | Left End |  | 46
120.9 | C1 | 51.9 | Bb0
166.9 | D1 | 143.9 | C#1 | Spacing between tone bars
212.9 | E1 | 189.9 | Eb1 | 23
258.9 | F1 | 281.9 | F#1
304.9 | G1 | 327.9 | Ab1 | Height between back of diatonic keys crossbar and back of accidental keys crossbar
350.9 | A1 | 373.9 | Bb1 | 62
396.9 | B1 | 465.9 | C#2
442.9 | C2 | 511.9 | Eb2
488.9 | D2 | 603.9 | F#2
534.9 | E2 | 649.9 | Ab2
580.9 | F2 | 695.9 | Bb2 | Note: All distances are measured relative to the left edge of the left columns, not the end of the crossbar
626.9 | G2 | 787.9 | C#3
672.9 | A2 | 833.9 | Eb3
718.9 | B2 | 925.9 | F#3
764.9 | C3 | 971.9 | Ab3
810.9 | D3 | 1017.9 | Bb3
856.9 | E3 | 1109.9 | C#4
902.9 | F3 | 1155.9 | Eb4
948.9 | G3 | 1247.9 | F#4
994.9 | A3 | 1293.9 | Ab4
1040.9 | B3 | 1339.9 | Bb4
1086.9 | C4
1132.9 | D4
1178.9 | E4
1224.9 | F4
1270.9 | G4
1316.9 | A4
1362.9 | B4
1408.9 | C5

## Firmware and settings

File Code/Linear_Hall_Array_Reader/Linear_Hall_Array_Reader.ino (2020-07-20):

/*
  Prototype code to read velocity from a large array of
  linear Hall effect sensors. This code is meant to be used for
  a MIDI carillon practice stand project, as a way to detect
  baton strikes.

  TO DO: Add calibration method in this script (for setting trigger values)
*/

#define N 12 // Keyboard chunk size (ie. number of notes)
#define TOP 1 // Top note (in MIDI notation) of keyboard chunk
#define BOTTOM 12 // Bottom note
#define LOOP_TIME 1 // Loop delay time in ms
#define SCALING 1 // Scaling factor for velocity
#define CHANNEL 0x90 // MIDI channel

// Global array of arrays
int global_array[N][3];
int pin_array[N] = {0,1,2,3,4,5,6,7,8,9,10,11};
int MIDI_array[N] = {0};
int trigger_values[N] = {0};

void setup() {
  // init global array
  for (int i = 0; i<3; i++){
    for (int j = 0; j<N; j++){
      global_array[j][i] = 1023;
    }
  }
  
  // init midi array
  for (int i = 0; i<N; i++){
    MIDI_array[N] = BOTTOM+i;
  }
  
  // init pins
  for (int i = 0; i < N; i++){
    pinMode(pin_array[i], INPUT);
    // Dunno if pullups are needed 
  }

  // Start serial stuff
  Serial1.begin(57600);
}

void loop() {
  
  // init vars
  int data = 1024;
  int velocity = 0;
  int delta = 0;

  // Loop through buffers
  for (int i = 0; i<3; i++){
    
    // Loop through reading each sensor
    for (int j = 0; j<N; j++){
      data = analogRead(j);
      global_array[j][i] = data;
      
      // If a sensor value is under the threshold...
      if(data <= trigger_values[j]){

        // Calculate delta using averaged buffer values
        if (i == 2){
          delta = ((global_array[j][2]-global_array[j][1])+(global_array[j][1]-global_array[j][0]))/2;
        }
        else if (i == 1){
          delta = ((global_array[j][1]-global_array[j][0])+(global_array[j][0]-global_array[j][2]))/2;
        }
        else if (i == 0){
          delta = ((global_array[j][0]-global_array[j][2])+(global_array[j][2]-global_array[j][1]))/2;
        }

        // If the delta isn't 0, map delta to velocity
        if (delta>0){
          velocity = delta*SCALING;

          // Then play the triggered note with the measured velocity
          playNote(MIDI_array[j], velocity);
        }
      }
    }

    // Wait before moving on to the next buffer (to allow time for baton to move)
    delay(LOOP_TIME);
  }
}

// Function for playing a carillon MIDI note (on then immediately off)
void playNote(int note, int volume){
  noteOn(CHANNEL, note, volume);
  noteOn(CHANNEL, note, 0x00);
}

// Function for building and sending MIDI messages over the serial interface 
void noteOn(int cmd, int pitch, int velocity) {
  Serial1.write(cmd);
  Serial1.write(pitch);
  Serial1.write(velocity);
}

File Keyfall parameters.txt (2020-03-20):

Keyhole at spreader: 77.5mm
Acceptable keyfall/pedalfall: 40-55mm

Accidental Keyheight: 24.92mm
Max accidental keyfall at spreader: 52.58
Accidental Felt thickness: 0 to 6.29mm
Accidental Imperial felt thickness: 0 to 1/4"

Diatonic keyheight: 19mm
Max diatonic keyfall at spreader: 58.5
Diatonic felt thickness: 1.75 to 9.25mm
Diatonic imperial felt thickness: 1/16" to 23/64"


Pedalhole at spreader: 85.68mm
Pedal thickness: 50.8mm
Max pedalfall at spreader: 34.88mm
Pedalfall at tip:

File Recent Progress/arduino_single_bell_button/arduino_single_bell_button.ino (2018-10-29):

int buttonInput = 5;
int buttonState = 0;
int i = 0;
void setup() {
  //  Set MIDI baud rate:
  pinMode(buttonInput, INPUT);
  digitalWrite(buttonInput, HIGH);
  Serial.begin(57600);
}

void loop() {
  buttonState = digitalRead(buttonInput);

    if(buttonState != HIGH&i==0){
    noteOn(0x90, 0x32, 0x45);
    delay(100);
    noteOn(0x90, 0x32, 0x00);
    i = 1;
    }
    if(buttonState == HIGH){
      i = 0;
    }

}

//  plays a MIDI note.  Doesn't check to see that
//  cmd is greater than 127, or that data values are  less than 127:
void noteOn(int cmd, int pitch, int velocity) {
  Serial.write(cmd);
  Serial.write(pitch);
  Serial.write(velocity);
}

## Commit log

2020-03-20 Added frame mechanical drawings
    [Baton test assembly.SLDASM, Keybase Piece 1.sldprt, Keybase Piece 2.sldprt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]
2020-03-20 Construction related files
    [BOM.xlsx, Keyfall parameters.txt, keypoint template.xlsx]
2020-03-20 Tone bar data and designs
    [Tone Bar Calculator.xlsx, tone bar mockup.SLDPRT, tone bar mockup_version 2.SLDPRT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]
2020-07-20 Added code for using Arduino Micro to read linear Hall effect sensors
2020-08-12 Add files via upload
    Added debouncing function and improved triggering when using SS49E hall sensors.
